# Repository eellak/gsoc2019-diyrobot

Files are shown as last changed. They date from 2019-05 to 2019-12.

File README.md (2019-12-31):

:rocket: GSOC 2019 - A DIY robot kit for educators 
===============

## Introduction
With this project I designed an easy to assembly and program, robot from scratch. The designs are 3D printable and all the electronics parts are easy to find in any electronic equipment store. The robot has the  Raspberry Pi 3+  as the main computer with Raspbian operating system combined with Jupyter Notebook as programing interface and a Node.js application as front-end main control page. You can program and control the robot through your browser using the Proteas wireless access point. 

[View the project on Google Summer of Code website](https://summerofcode.withgoogle.com/projects/#6536613096587264).

You can see the detailed timeline [here](https://github.com/eellak/gsoc2019-diyrobot/blob/master/gsoc-timeline.md).

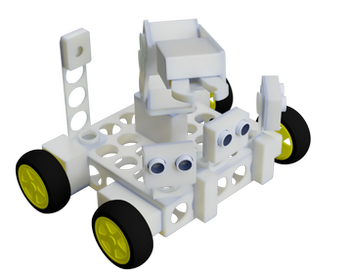
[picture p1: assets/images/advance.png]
proteas robot advance


### Proteas robot teaser video

(http://www.youtube.com/watch?v=83zVe_P6pcM "")

Final Report
------------

You can visit this [gist](https://gist.github.com/chronis10/9d069c56b3df9c92693ac8d24270a62a) that summarizes in a few words, the work which was done during the Google Summer of Code working period.

Synopsis
--------

With this project you can construct a modular robot, easy to use with cheap electronic parts and 3D printed parts. The procedure to construct the robot is explained detailed on the [Wiki](https://github.com/eellak/gsoc2019-diyrobot/wiki) of the project. The main procedure is:

1. Read the wiki and choose the type of robot you want
2. Gather all the needed electronic parts
3. Print the parts
4. Preassembly the blocks
5. Burn the custom Raspbian image and load it to the Raspberry PI
6. Assembly the robot
7. Power on the robot 
8. Connect to proteas network and have fun.

Challenges -> Problems -> Solutions
--------

The main challenge of the project was the requirement to avoided the usage of tools on the assembly stage. The first days of the project I designed and tested about ten different designs of the socket system. Another problem was the voltages of the electronic parts, most of the parts are designed to work with the Arduino 5V voltages but the Raspberry Pi voltages are 3V and for that reason used a Bidirectional Logic Level Converter.  Also the investigation of a stable and capable power source  was crucial because nobody wants a robot with short working time, finally selected a custom build power block (BMS, Li-ion batteries and stepdown circuit) which offers excellent performance, recharging capability, usage of the robot with external power supply and long working time. Finally because the robot needed to be easy to programme form people with low experience with programming, decided to use a object oriented way. The code for the electronic parts in some cases it was complicated for a new user and using the object oriented way the code transformed from 50 lines to 3 lines easy to understand and use code. 

GSoC Deliverables
------------

1. 3D printed parts ready to print
2. Python library for easy usage and control of the robot
3. Integration with Jupyter
4. Easy way to access the robot
5. Custom Raspbian image with OpenCV, Jupyter, Node.js, Python libraries, instructions and configuration intergraded.
6. Extensive instruction for the assembly and usage
7. Jupyter Notebooks with examples and educational material

Future Work
------------

There is still a lot work that may be done, in order the Proteas robot to be a direct competitive to any commercial alternative on education robotics and I believe, with the support of the Open Source community, that goal can be reached. Feel free, to contribute and participate on that project, any suggestion and improvement are welcomed. 

Some thoughts for future work:

1. Support of analogue sensors
2. More 3D printed components
3. More electronic sensors support
4. Improvements on designs
5. Integration with Scratch, Node-RED
6. Compatibility with Arduino
7. Better wireless connection 
8. Companion app for Android/IOS
9. Custom build PCB for easy connection of the electronic components

### Student

* [Christos Chronis](https://github.com/chronis10)

### GSoC Mentors

* Iraklis Varlamis
* Theodoros Karounos
* Konstantinos Kalovrektis

### Organization :  Open Technologies Alliance - GFOSS 

<br />The 3D designs , educational material and text is licensed under a  <a rel="license" href="http://creativecommons.org/licenses/by-nc/4.0/">Creative Commons Attribution-ShareAlike 4.0 International License</a>

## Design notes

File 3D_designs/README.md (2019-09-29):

# The designs of the DIY-Robot kit

Here you can find all the stl files for the kit. For instructions and images visit the [Wiki](https://github.com/eellak/gsoc2019-diyrobot/wiki)  of the repository . 

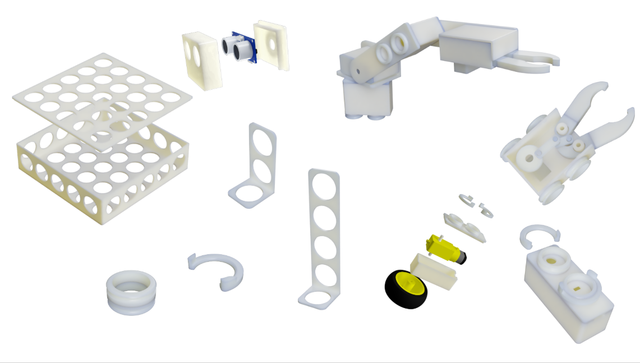
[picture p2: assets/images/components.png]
components


* Socket System templates 
  * Connection System between components blocks :white_check_mark:
  * Lock System between for components blocks :white_check_mark:
  * Raspberry Pi 3 self lock base :white_check_mark:
  * L298N Dual H-Bridge self lock base :white_check_mark:
* Motor Block 
  * Top part :white_check_mark:
  * Bottom part :white_check_mark:
* Free rotation modules
  * Metal Ball Caster :white_check_mark:
  * Free rotation wheel module :white_check_mark:
* Main body 
  * Top part :white_check_mark:
  * Bottom part tall :white_check_mark:
  * Bottom part short:white_check_mark:
* Boards modules
  * Raspberry Pi 3 self lock base with male socket :white_check_mark:
  * L298N Dual H-Bridge self lock base with male socket :white_check_mark:
  * Power block 
  * Battery block
* Wire grouping socket 
  
  * 8 Pin expansion suitable for GND and VCC  :white_check_mark:
  * 10 cables management component (thin cables) :white_check_mark:
  * 10 cables management component (normal cables) :white_check_mark:
  * 10 cables management component (mixed cables) :white_check_mark:
* Servo Blocks
  
  * SG-5010 Servo :white_check_mark:
* Arm parts
  * Rotation base :white_check_mark:
  * Arm extension servo head socket :white_check_mark:
  * Robotic Arm Gripper :white_check_mark:
* Sensors Blocks
  * Raspberry Pi Camera Block :white_check_mark:
  
  * Ultrasonic sensor HC-SR04 :white_check_mark:
  
  * IR Infrared Obstacle :white_check_mark:
  
  * Sensor extender 2 socket L shape:white_check_mark:
  
  * Sensor extender 4 socket L shape:white_check_mark:
  
  * Dual male connector for Sensor extenders :white_check_mark:
  
  * Breadboard module :white_check_mark:
  
  * Magic Super-Mini-Breadboard :white_check_mark:
  
  * Nokia 5110 LCD screen module :white_check_mark:
  
  * Optical odometer HC-020K block:white_check_mark:
  
  * Internal Optical odometer HC-020K block:white_check_mark:

## Explanation of the marks
* :warning: Under Construction part, not ready for printing yet.
* :white_check_mark: Ready for printing.
* :construction: Upcoming release

<br />The 3D designs , educational material and text is licensed under a  <a rel="license" href="http://creativecommons.org/licenses/by-nc/4.0/">Creative Commons Attribution-ShareAlike 4.0 International License</a>

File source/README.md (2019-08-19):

# The mind of the Robot

Here you can find all the needed files (python libraries and scripts) for a smooth deployment. 

For instructions visit the [Wiki](https://github.com/eellak/gsoc2019-diyrobot/wiki) of the repository

An overview of my programming stuck.
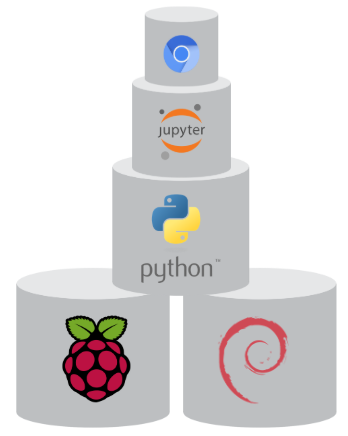
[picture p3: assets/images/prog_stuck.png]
prog stuck


* Python robot library :white_check_mark::
  * Buzzer class :white_check_mark:
  * Dc motor class :white_check_mark:
  * Optical odometer class :white_check_mark:
  * Obstacle IR sensor  class :white_check_mark:
  * Servo motor class :white_check_mark:
  * Nokia 5110 screen :white_check_mark:
  * MPU6050 accelerometer :white_check_mark:
  * Ultrasonic sensor :white_check_mark:
  * General input class (every sensor with digital output eg. light sensor) :white_check_mark:
  * General output class (led and every sensor with digital input eg.  relay shield) :white_check_mark:
  * Button class with software Pull Down parameter enabled :white_check_mark:
  * Timer class for usage on PID,logs or every usage with time elapsed needs :white_check_mark:
  * Log data class store data for plot or evaluation :white_check_mark:
  * Make csv class save measurements to csv :white_check_mark:
  * PID class :white_check_mark:
  * Inverse Kinematics for 2-DOF robotic arm :white_check_mark:
  
* Computer Vision library :white_check_mark:
  * Capture image class :white_check_mark:
  * Image preview class on Jupyter notebook :white_check_mark:
  * Aruco artifacts class :white_check_mark:
  * Line follower class (camera mode) :white_check_mark:
  * Face detection class  :white_check_mark:
  * Follow the target class (line,face or Aruco artifact) :white_check_mark:
  * Approach the target class (face or Aruco artifact) :white_check_mark:
  
* Notebooks section
  * Courses and Examples :white_check_mark:

* Browser interface
  * Node.js app for the robot management from your browser.:white_check_mark:

## :exclamation: **Important Notice** :exclamation:
:cop: The robot fully comply with the three laws of robotics:

**Asimov's Laws**

  * **First Law:** A robot may not injure a human being or, through inaction, allow a human being to come to harm.
  * **Second Law:** A robot must obey the orders given it by human beings except where such orders would conflict with the First Law.
  * **Third Law:** A robot must protect its own existence as long as such protection does not conflict with the First or Second Laws.

## Explanation of the marks
* :warning: Under Construction, probably errors not ready for use.
* :white_check_mark: Ready for usage.
* :construction: Upcoming release

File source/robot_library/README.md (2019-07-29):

## GSOC 2019 - A DIY robot kit for educators

The proteas library is a python robotics library for 
Raspberry Pi. This library created for the "GSOC 2019 - A DIY robot kit for educators" 
by Christos Chronis. This library mainly designed to work along the Jupyter Notebook
but works fine direct from any python script. You can easly control all the electronics
parts of a robot with minimun requirement the GPIO pin number. In the library you can also find 
some applications of computer vision with OpenCV, such as face detection, arruco artifact detection
e.t.c.. More informations on https://github.com/eellak/gsoc2019-diyrobot.

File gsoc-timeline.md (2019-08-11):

## :calendar: Timeline

The implementation details follow, organized by [GSoC timeline](https://developers.google.com/open-source/gsoc/timeline).

## Phase 1 (May 27 - Jun 28)

The proper electronic parts selected for that project and  designed,printed and tested the 3D parts of the robot in a modular way with a tool-less philosophy. 

- Selection of electronic parts
- 3D designs :triangular_ruler:
- Parts printing stage
- Functionality tests of the parts
- Robot Assembly :wrench:

## Phase 2 (Jun 29 - Jul 26)

New libraries created for the communication between hardware-software.  A object oriented way for programming selected and the integration with Jupyter completed. 

- Control library
- Vision library
- OpenCV integration
- Special control and functionality library (e.x. PID Controller)
- Jupyter Notebook integration
- Wireless access, control and programming of the program achieved 

## Phase 3 (Jul 27 - Aug 26)

All the needed preparations completed  for easy deployment of software and material for the courses, user manuals and instructions created.

- Modifications of Rasbian image
- Courses on Jupyter Notebook (e.x. Line Follower robot)
- PDFs with extensive instructions for the assembly and usage of the robot
- Final debugging
- Wiki page created

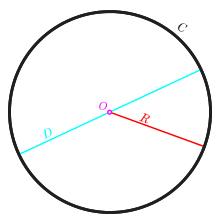
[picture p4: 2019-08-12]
source/notebooks/Courses/Distance calculation based on circle theory/images/circle.png

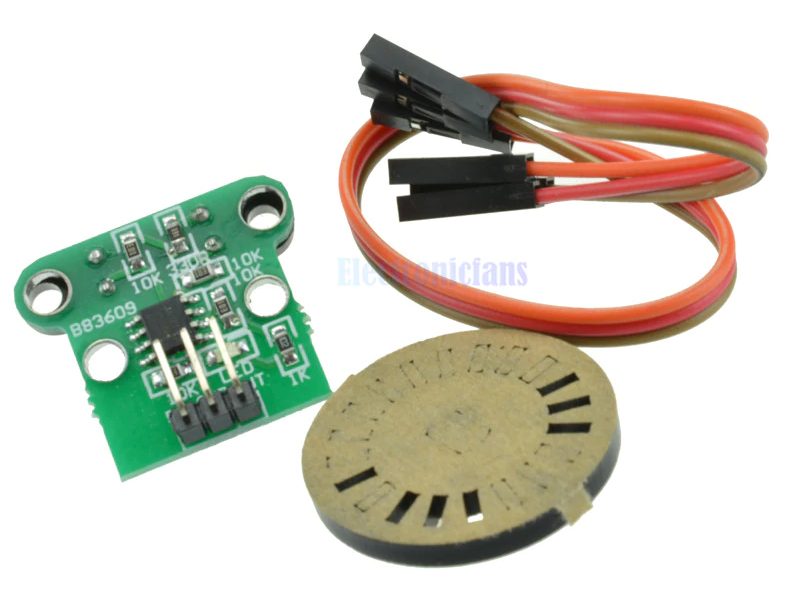
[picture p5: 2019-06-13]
3D_designs/odometers/optical_odometer_block/HC-020K.png

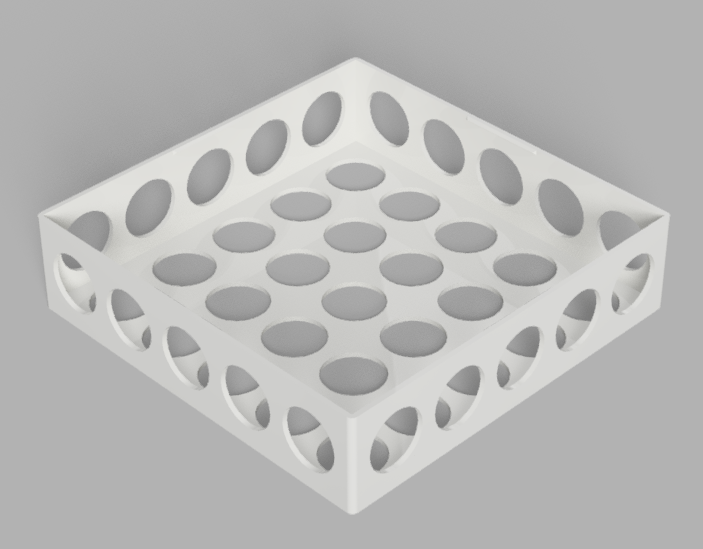
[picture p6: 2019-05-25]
3D_designs/base/main_body_bottom_short_v1.png

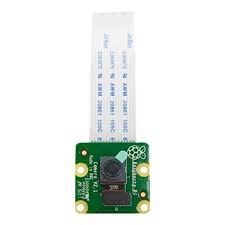
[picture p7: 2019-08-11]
3D_designs/raspberry_pi_camera_block/raspberry pi camera.jpg

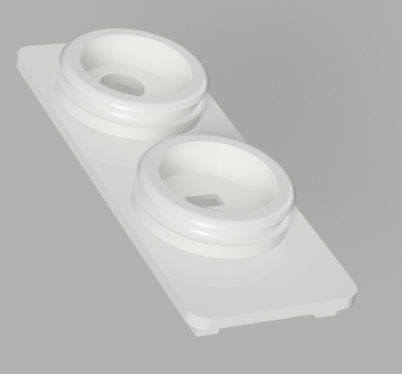
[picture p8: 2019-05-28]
3D_designs/motor_block/motor_block_top_v1.png

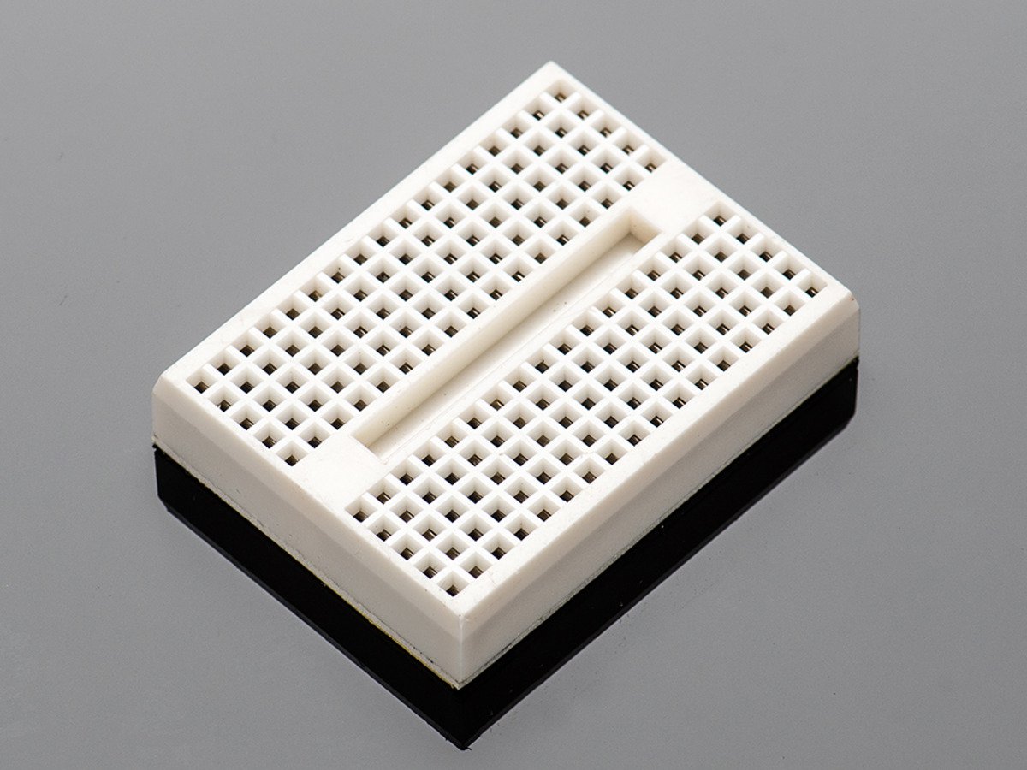
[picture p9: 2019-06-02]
3D_designs/breadboard_blocks/small_breadboard_block/breadboard.jpg

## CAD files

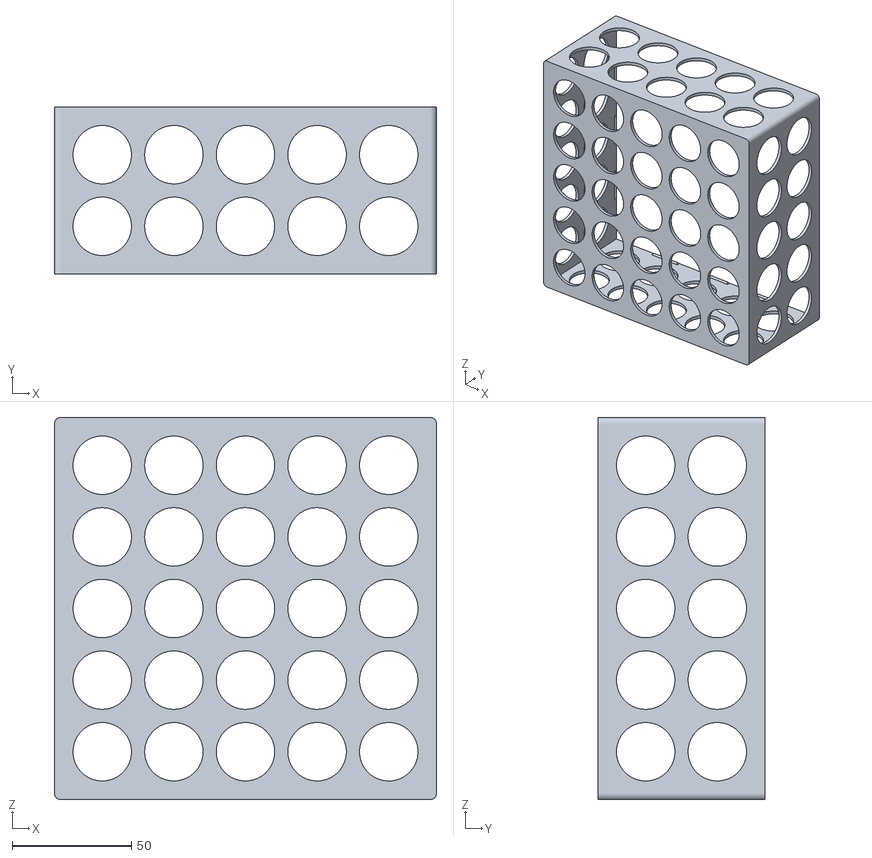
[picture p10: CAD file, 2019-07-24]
3D_designs/base/main_body_bottom_tall_v1.stl
160.0 x 70.0 x 160.0

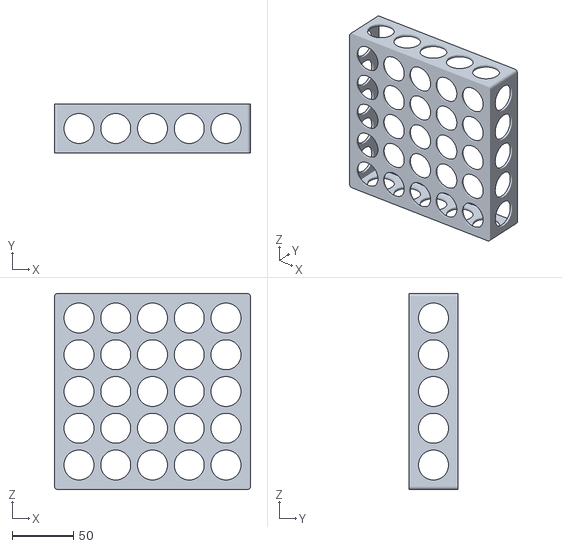
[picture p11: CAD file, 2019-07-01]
3D_designs/base/main_body_bottom_short_v1.stl
160.0 x 40.0 x 160.0

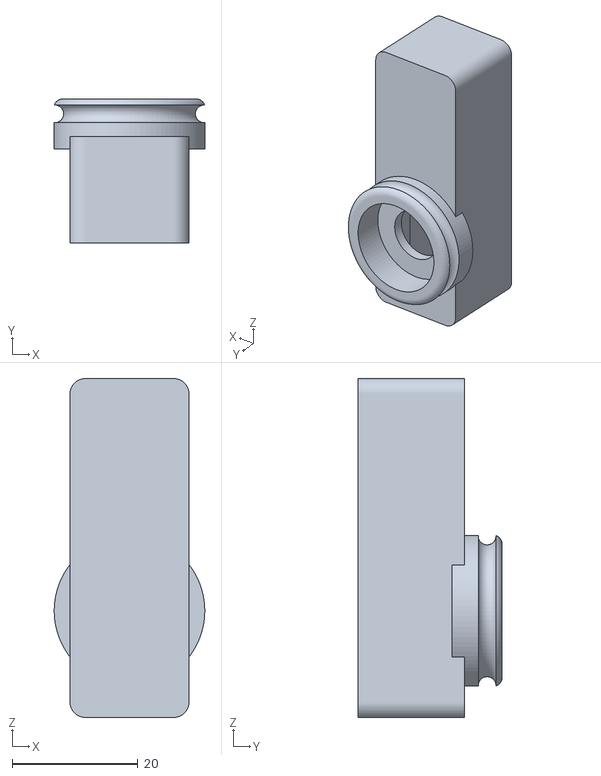
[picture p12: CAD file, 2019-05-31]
3D_designs/ir_obstacle_sensor_block/ir_block_assembled_v1.stl
24.0 x 23.0 x 54.0

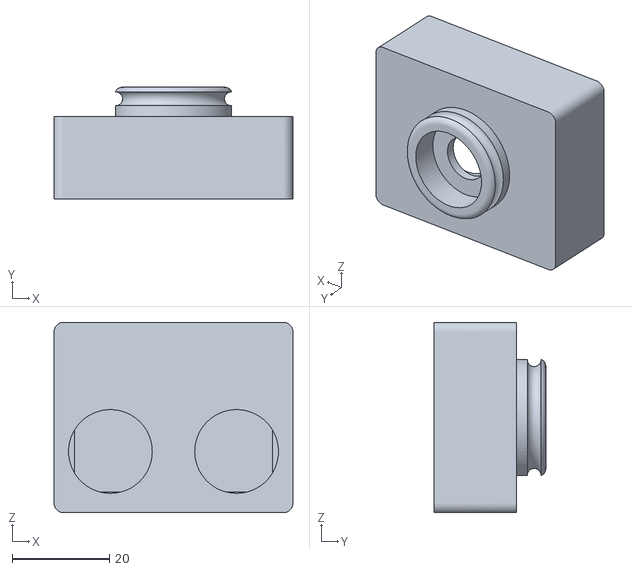
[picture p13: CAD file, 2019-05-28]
3D_designs/ultrasonic_sensor_block/HC-SR04_ultrasonic_block_assembled_v1.stl
49.2 x 23.0 x 39.2

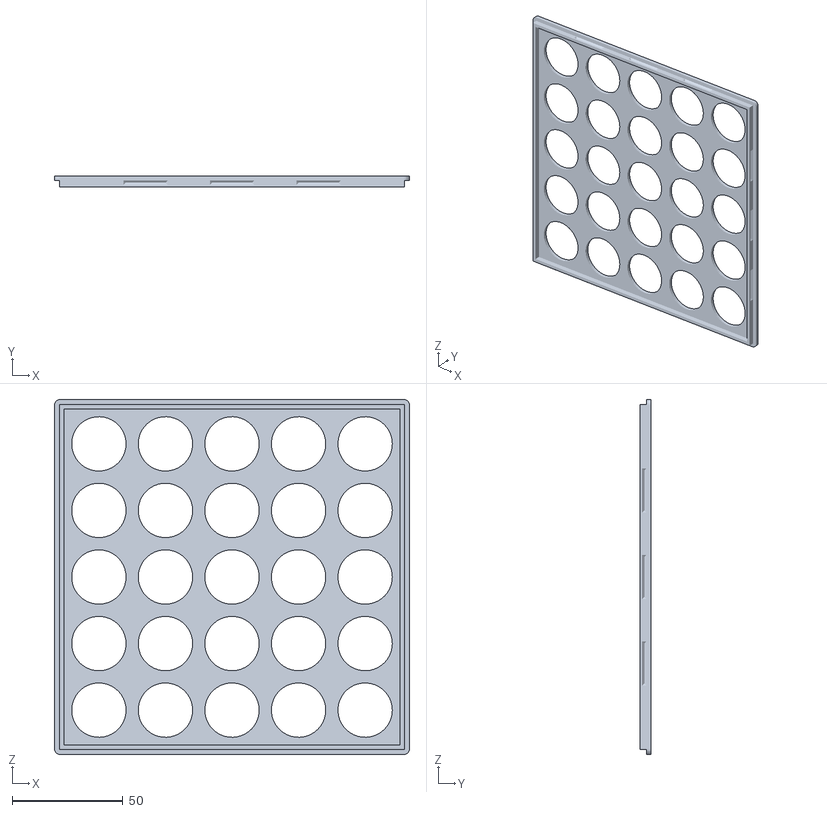
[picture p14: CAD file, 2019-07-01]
3D_designs/base/main_body_top_v1.stl
160.0 x 5.00 x 160.0

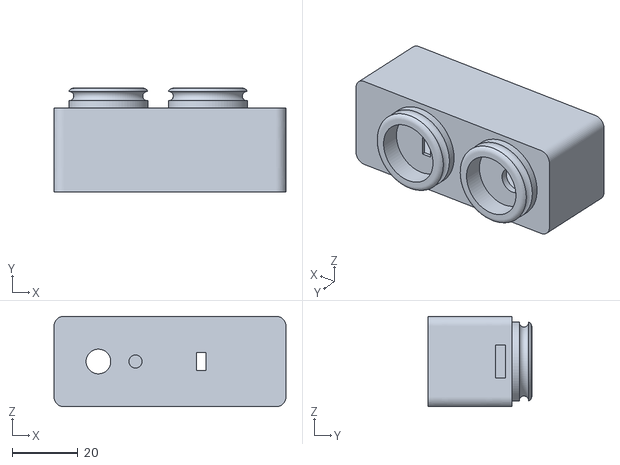
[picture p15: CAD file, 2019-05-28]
3D_designs/motor_block/motor_block_assembled_v1.stl
70.5 x 31.5 x 27.5

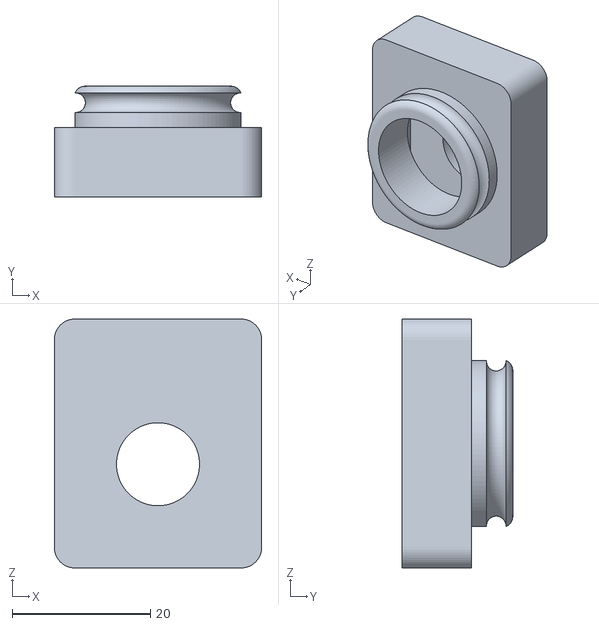
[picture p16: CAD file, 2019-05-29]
3D_designs/raspberry_pi_camera_block/camera_block_assembled_v1.stl
30.0 x 16.0 x 36.0

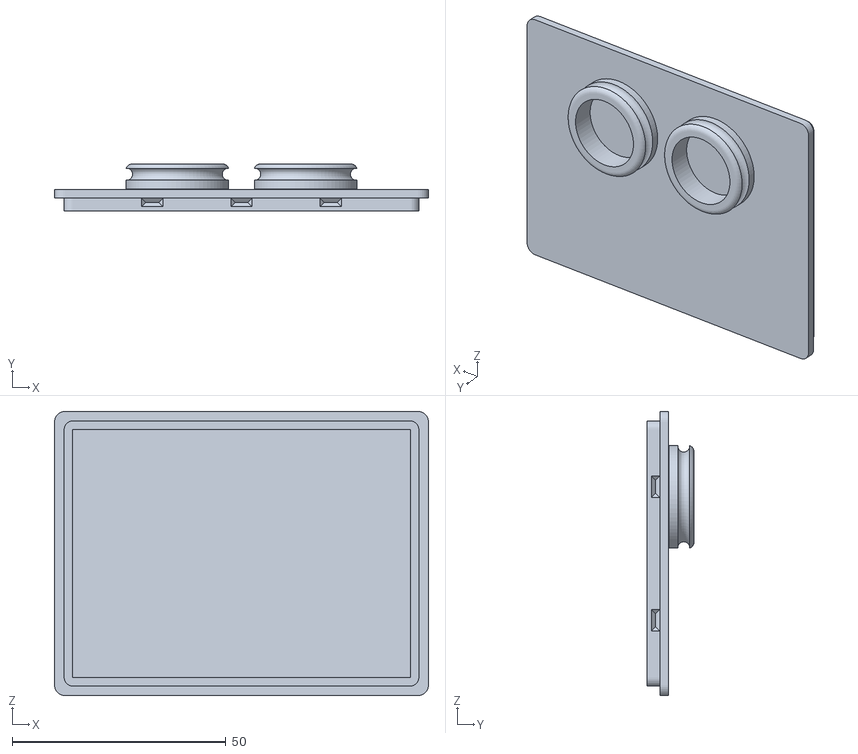
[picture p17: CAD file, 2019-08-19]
3D_designs/battery_block/battery_block_top_v1.stl
87.5 x 11.0 x 66.5

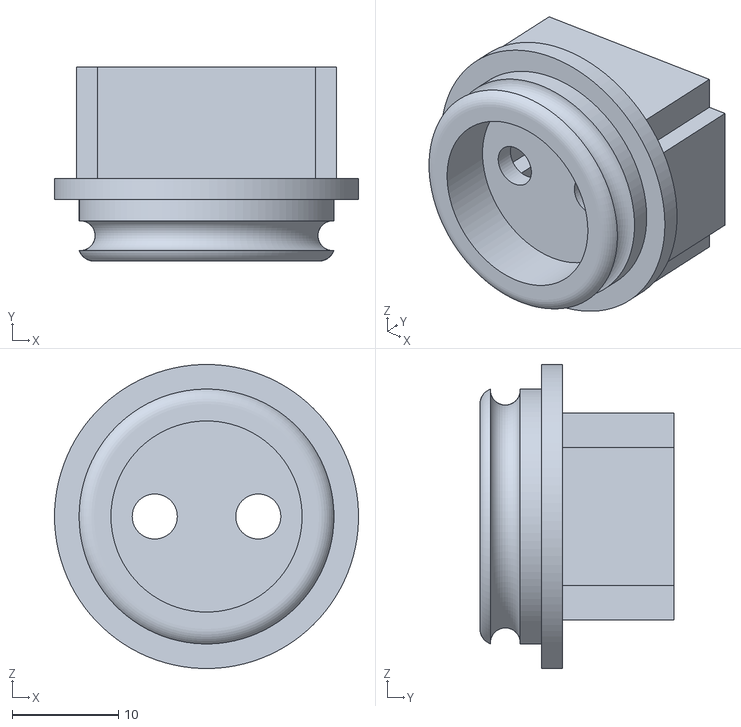
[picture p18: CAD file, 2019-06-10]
3D_designs/breadboard_blocks/mini_breadboard_block/mini_breadboard v1.stl
28.6 x 18.3 x 28.6

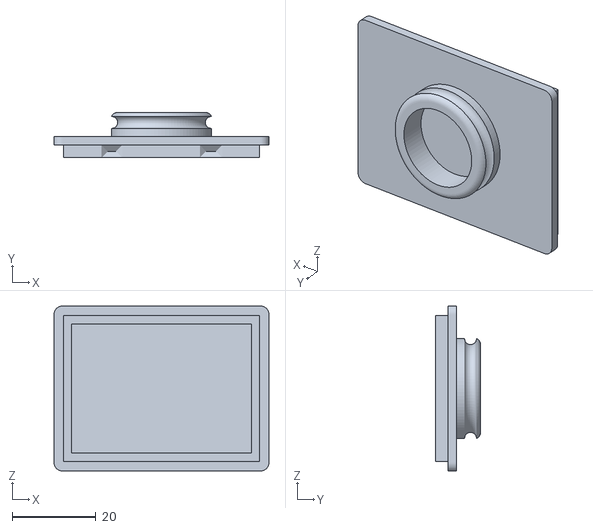
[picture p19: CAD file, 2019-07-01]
3D_designs/breadboard_blocks/small_breadboard_block/breadboard_module_top_v1.stl
51.5 x 10.8 x 39.5

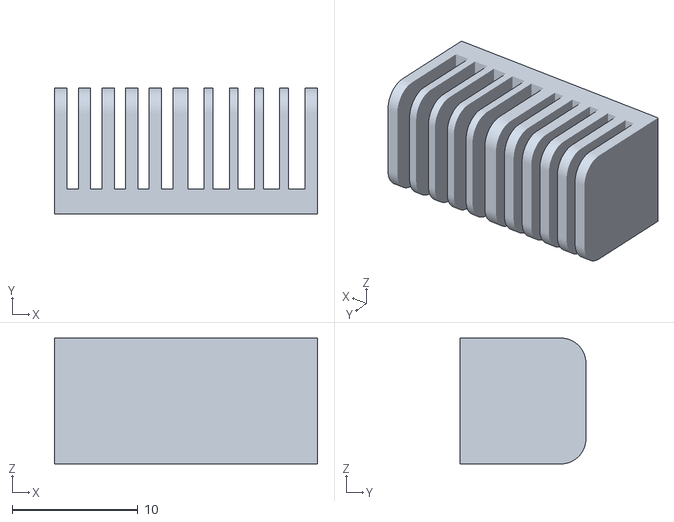
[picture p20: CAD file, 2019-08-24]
3D_designs/cable_management/mixed_cables.stl
20.9 x 10.0 x 10.0

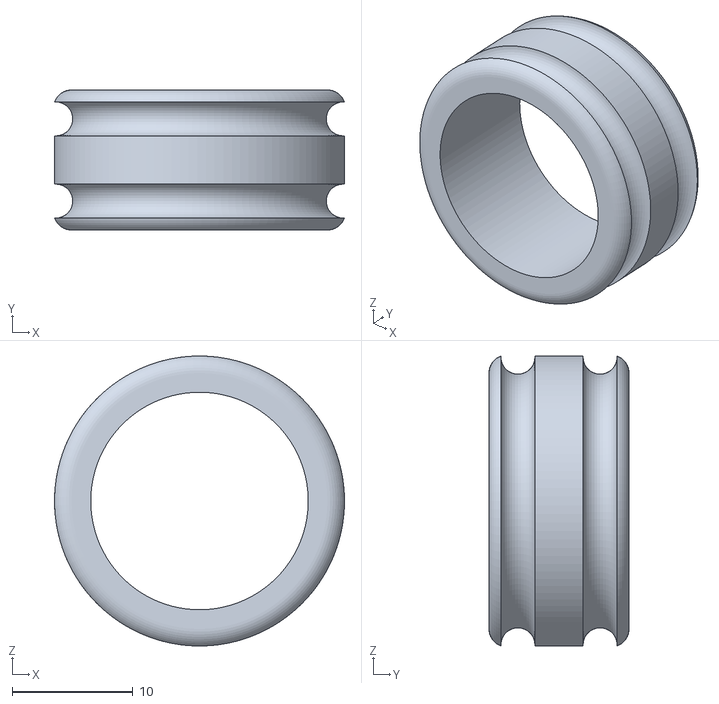
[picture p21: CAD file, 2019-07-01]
3D_designs/expansion_parts/dual_male_head_v1.stl
24.0 x 11.6 x 24.0

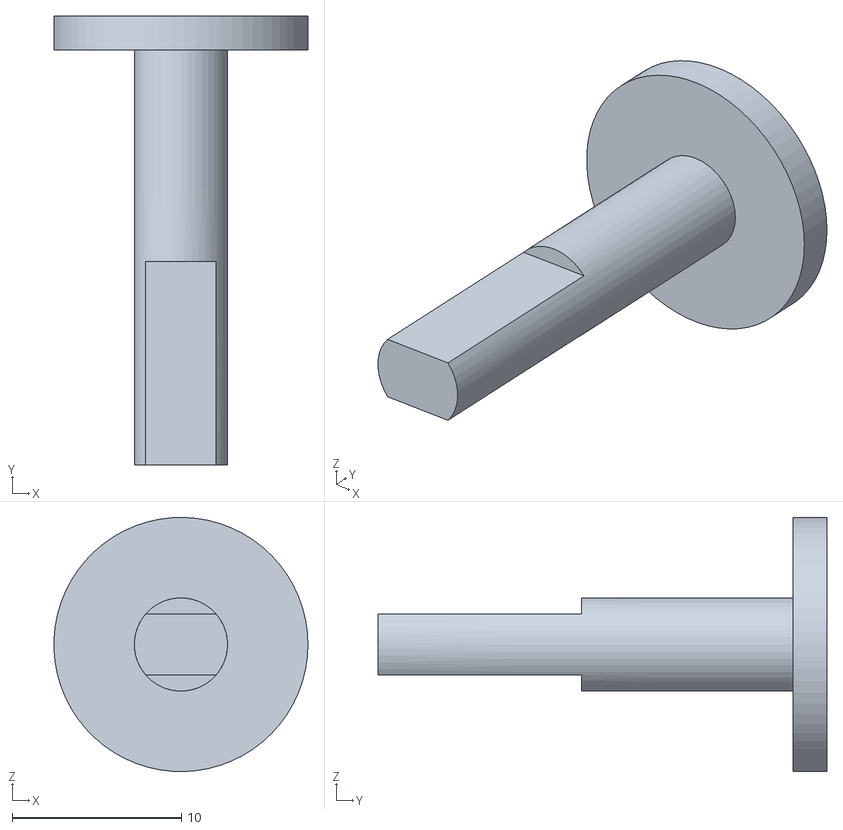
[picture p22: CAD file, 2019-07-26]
3D_designs/free_rotation_parts/free_rotation_wheel_block/shaft_v1.stl
15.0 x 26.5 x 15.0

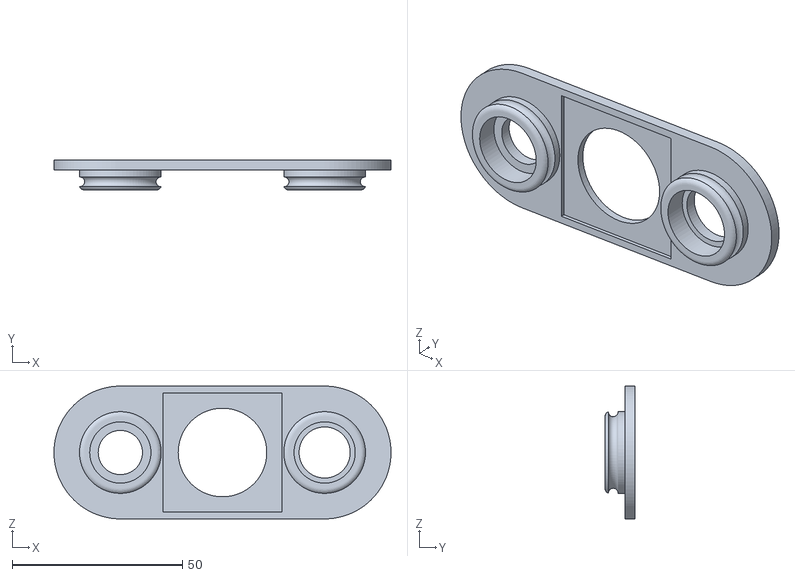
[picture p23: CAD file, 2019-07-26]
3D_designs/free_rotation_parts/metal_ball_caster_block/metal_ball_caster_v1.stl
99.0 x 8.80 x 39.0

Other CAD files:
3D_designs/ir_obstacle_sensor_block/ir_block_top_v1.stl
3D_designs/motor_block/motor_block_bottom_v1.stl
3D_designs/motor_driver_base/L298N_Dual_H-Bridge_clip_module_v1.stl
3D_designs/multiconnector_module/multiconnector_module_v1.stl
3D_designs/battery_block/battery_block_bottom_v1.stl
3D_designs/breadboard_blocks/small_breadboard_block/breadboard_module_bottom_v1.stl
3D_designs/cable_management/normal_cables.stl
3D_designs/cable_management/thin_cables.stl
3D_designs/expansion_parts/sensor_extender_tall_v1.stl
3D_designs/expansion_parts/sensor_extender_v1.stl
3D_designs/free_rotation_parts/free_rotation_wheel_block/free_rotation_wheel_block_v1.stl
3D_designs/ir_obstacle_sensor_block/ir_block_bottom_v1.stl
3D_designs/motor_block/motor_block_top_v1.stl
3D_designs/nokia_5110_screen_block/screen_block_bottom_v1.stl
3D_designs/nokia_5110_screen_block/screen_block_top_v1.stl
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

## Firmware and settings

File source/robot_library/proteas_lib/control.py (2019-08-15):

import time
import RPi.GPIO as GPIO
import math
import time
import csv
import Adafruit_Nokia_LCD as LCD
import Adafruit_GPIO.SPI as SPI
from PIL import ImageFont,ImageDraw,Image
from netifaces import interfaces, ifaddresses, AF_INET
import matplotlib.pyplot as plt
from mpu6050 import mpu6050
from random import randrange
import smbus	

# Hardware section
class gen_output():
	'''
	Class gen_output(pin)
	Deafult pin 5
	Functions:
	set_on() set High the output pin
	set_off() set Low the output pin
	'''
	def __init__(self,pin=5):
		self.pin = pin
		GPIO.setup(self.pin,GPIO.OUT)
		GPIO.output(self.pin, False)
	def set_on(self):
		GPIO.output(self.pin, True)
	def set_off(self):
		GPIO.output(self.pin, False)	


class gen_input():
	'''
	Class gen_input(pin)
	Default pin 4
	Functions:
	get_state() return True/False
	'''
	def __init__(self,pin=4):
		self.pin = pin
		GPIO.setup(self.pin,GPIO.IN)
	def get_state(self):
		return GPIO.input(self.pin)

class button():
	'''
	Class button(pin)
	Default pin 18
	Software pull down activated
	Functions:
	get_state() return True/False
	'''
	def __init__(self,pin=18):
		self.pin = pin
		GPIO.setup(self.pin,GPIO.IN,pull_up_down=GPIO.PUD_UP)
	def get_state(self):
		return GPIO.input(self.pin)


class ultrasonic_sensor():
	'''
	Class ultrasonic_sensor(echo_pin,trig_pin)
	Default pins echo_pin=14,trig_pin=15
	Functions:
	get_distance() return distance on cm
	'''
	def __init__(self,echo_pin=14,trig_pin=15):
		self.echo_pin = echo_pin
		self.trig_pin = trig_pin
		GPIO.setup(self.echo_pin,GPIO.IN)
		GPIO.setup(self.trig_pin,GPIO.OUT)
		GPIO.output(self.trig_pin, False)
	def get_distance(self):

		GPIO.output(self.trig_pin, True)
		time.sleep(0.00001)
		GPIO.output(self.trig_pin, False)
		StartTime = time.time()
		StopTime = time.time()
		while GPIO.input(self.echo_pin) == 0 :
			StartTime = time.time()

		while GPIO.input(self.echo_pin) == 1:
			StopTime = time.time()
		TimeElapsed = StopTime - StartTime
		distance = (TimeElapsed * 34300) / 2
		return distance

class screen():
	'''
	Class screen(SCLK = 21,DIN = 20,DC = 16,RST =7,CS = 12)
	Functions:
	clear_scrn() Clears the screen
	show_text(text,x=0,y=0) Prints text in the screen
	ip_screen() Prints the current ip
	print_text(text_list) Get a list input of 5 item and print every item in a line
	show_image(path) Draw a graph in png from the images/ path
	'''
	def __init__(self,SCLK = 21,DIN = 20,DC = 16,RST =7,CS = 12):
		self.SCLK = SCLK
		self.DIN = DIN
		self.DC = DC
		self.RST = RST
		self.CS = CS
		self.disp = LCD.PCD8544(DC, RST, SCLK, DIN, CS)
		self.disp.begin(contrast=60)
		self.font = ImageFont.load_default() #ImageFont.truetype('Minecraftia.ttf', 8)
		self.clear_scrn()
		self.empty_canvas()

	def clear_scrn(self):
		self.disp.clear()
		self.disp.display()
	def empty_canvas(self):
		self.canvas= Image.new('1', (LCD.LCDWIDTH, LCD.LCDHEIGHT))
		self.draw = ImageDraw.Draw(self.canvas)
		self.draw.rectangle((0,0,LCD.LCDWIDTH,LCD.LCDHEIGHT), outline=255, fill=255)

	def show_text(self,text,x=0,y=0):
		self.draw.text((x,y),text, font=self.font)

	def show_canvas(self):
		self.disp.image(self.canvas)
		self.disp.display()
	def ip_screen(self):
		self.clear_scrn()
		self.empty_canvas()
		self.show_text("Proteas Robot")
		ipl = get_ip()
		self.show_text("Connect to:",0,9)
		self.show_text("http://",0,19)
		self.show_text(ipl[-1],0,29)
		self.show_text(":8080",0,39)
		self.show_canvas()

	def print_text(self,text_list):
		self.clear_scrn()
		self.empty_canvas()
		posy = 0
		for i in range(0,5):
			temp  = text_list[i]
			if isinstance(temp,int) or isinstance(temp,float):
				temp = str(temp)
			self.show_text(temp,0,posy)
			posy += 9
		self.show_canvas()
	def show_image(self,path):
		path = "images/" +path
		self.clear_scrn()
		im = Image.open(path)
		self.canvas = im.resize((LCD.LCDWIDTH, LCD.LCDHEIGHT), Image.ANTIALIAS).convert('1')
		self.show_canvas()


class accelerometer():
	'''
	Class accelerometer(address=0x68)
	Functions:
	get_acceleration(dimension = "all") with "parameter return dictionary with x,y,z acceleration for a specific dimension give as parameter "x","y","z" return value
	get_gyro(dimension = "all") with "parameter return dictionary with x,y,z acceleration for a specific dimension give as parameter "x","y","z" return value
	'''
	def __init__(self,address=0x68):
		self.sensor = mpu6050(address)
	def get_acceleration(self,dimension = "all" ):
		accel = self.sensor.get_accel_data()
		if dimension == "all":
			return accel
		elif dimension == "x" or dimension == "y" or dimension == "z":
			return accel[dimension]
		else:
			print("Dimension not recognized!!")
			return 0
	def get_gyro(self,dimension = "all" ):
		gyro = self.sensor.get_gyro_data()
		if dimension == "all":
			return gyro
		elif dimension == "x" or dimension == "y" or dimension == "z":
			return gyro[dimension]
		else:
			print("Dimension not recognized!!")
			return 0




class buzzer():
	'''
	Class buzzer(pin,freq=1500,dc=50)
	Functions:
	beep() Short tone
	timer(count) Timer function with wait and for every 1 sec makes a tone
	'''
	def __init__(self,pin,freq=1500,dc=50):
		GPIO.setup(pin,GPIO.OUT)
		self.buz = GPIO.PWM(pin,freq)
		self.freq = freq
		self.dc = dc
		self.buz.start(0)
	def beep(self):
		self.buz.ChangeDutyCycle(self.dc)
		time.sleep(0.1)
		self.buz.ChangeDutyCycle(0)
	def timer(self,count):
		print("Timer start for {}".format(count))
		for i in range(1,count+1):
			self.buz.ChangeDutyCycle(self.dc)
			time.sleep(0.5)
			self.buz.ChangeDutyCycle(0)
			time.sleep(0.5)
			print("{} sec".format(i))
		print("Timer finished")
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

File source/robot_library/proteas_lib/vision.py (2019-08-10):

import numpy as np
import cv2, PIL
from cv2 import aruco
import matplotlib.pyplot as plt
import matplotlib as mpl
from IPython.display import display, HTML,clear_output
import PIL.Image

class aruco_find():
	def __init__(self):
		self.aruco_dict = aruco.Dictionary_get(aruco.DICT_6X6_250)
		self.parameters =  aruco.DetectorParameters_create()
		self.ids = []
		self.corners = []
		self.cx = 0
		self.cy = 0
		self.width = 0
		self.height=0		
	def to_gray(self,image):
		return cv2.cvtColor(image, cv2.COLOR_BGR2GRAY)
	def detect(self,image):
		corners, ids, rejectedImgPoints = aruco.detectMarkers(image, self.aruco_dict, parameters=self.parameters)
		return corners, ids, rejectedImgPoints
	def mark_image(self,image,corners, ids):
		if ids is not None:
			self.ids = self.marks_to_list(ids)
			self.corners = self.marks_to_list(corners)
		else:
			self.ids = []
			self.corners = []
		image_marked = aruco.drawDetectedMarkers(image.copy(), corners, ids)
		return image_marked
	def detect_artifacts(self,image):
		gray = self.to_gray(image)
		corners, ids, rejectedImgPoints = self.detect(gray)
		final = self.mark_image(image,corners, ids)
		return final
	def marks_to_list(self,nplist):
		temp = []
		nplist = np.array(nplist).tolist()
		for item in nplist:
			temp.append(item[0])
		return temp
	def find(self,ar_id):
		if len(self.ids)>0:
			if ar_id in self.ids:
				i = self.ids.index(ar_id)
				x1=self.corners[i][0][0]
				x2=self.corners[i][1][0]
				y1=self.corners[i][0][1]
				y2=self.corners[i][3][1]
				self.cx = int(((x2-x1)/2)+x1)
				self.cy = int(((y2-y1)/2)+y1)
				self.width = x2-x1
				self.height = y2-y1		
		else:
				self.cx = 0
				self.cy = 0
				self.width = 0
				self.height = 0
	def mark_frame(self,frame):
		height, width, channels = frame.shape
		cv2.line(frame,(self.cx,0),(self.cx,height),(255,0,0),1)
		cv2.line(frame,(0,self.cy),(width,self.cy),(255,0,0),1)
		return frame
	def get_pos(self):
		return self.cx,self.cy
	def get_rect(self):
		return self.width,self.height

class camera():	
	def __init__(self,camera=0):
		self.camera = camera
		self.cap = cv2.VideoCapture(self.camera)		
	def take_frame(self):
		ret, frame = self.cap.read()
		return frame
	def stop(self):
		self.cap.release()

class show_image():
	def __init__(self,jupyter=True):
		self.jupyter = jupyter
	def cpreview(self,frame):
		cv2.imshow('frame',frame)
		cv2.waitKey(1) 
	def jpreview(self,frame):
		im = cv2.cvtColor(frame, cv2.COLOR_BGR2RGB)
		display(PIL.Image.fromarray(im))		
		clear_output(wait=True)	
	def preview(self,frame):
		if self.jupyter:
			self.jpreview(frame)
		else:
			self.cpreview(frame)
	def clear(self):
		if self.jupyter:	
			clear_output(wait=True)	
		else:
			cv2.destroyAllWindows()

class face_detection():
	def __init__(self):
		cascPath = '/home/pi/ext/haarcascade_frontalface_default.xml'
		self.faceCascade = cv2.CascadeClassifier(cascPath)
		self.cx = 0
		self.cy = 0
		self.width = 0
		self.height=0
		self.faces_num = 0
	def detect_face(self,frame):
		gray = cv2.cvtColor(frame, cv2.COLOR_BGR2GRAY)
		faces = self.faceCascade.detectMultiScale(gray,
		scaleFactor=1.1,
		minNeighbors=5,
		minSize=(30, 30),
		flags=cv2.CASCADE_SCALE_IMAGE)
		if len(faces) > 0:
			self.faces_num = len(faces)
			(x,y,w,h)= faces[0]
			cv2.rectangle(frame, (x, y), (x+w, y+h), (0, 255, 0), 2)
			self.cx = int(((w/2)+x))
			self.cy = int(((h/2)+y))
			self.width = w
			self.height = h
			fheight, fwidth, channels = frame.shape
			cv2.line(frame,(self.cx,0),(self.cx,fwidth),(255,0,0),1)
			cv2.line(frame,(0,self.cy),(fwidth,self.cy),(255,0,0),1)
			cv2.circle(frame,(self.cx, self.cy), 5, (0,255,0), -1)
		else:
			self.faces_num = 0
			self.cx = 0
			self.cy = 0
			self.width = 0
			self.height = 0
		return frame
	def get_faces(self):
		return self.faces_num
	def get_pos(self):
		return self.cx,self.cy
	def get_rect(self):
		return self.width,self.height

class robot_center():
	def __init__(self,width=640):
		self.width = width
		self.step = int(width/5)
		self.w1 = self.step*2
		self.w2 = self.step*3
		
	def direction(self,posx):
		if posx >0 and posx < self.w1:
			print("Go Right")
			return 2
		elif posx >self.w2 and posx < self.width:
			print("Go Left")
			return 1
		elif posx == 0:
			print("No detection")
			return -1
		else:
			print("Stay")
			return 0

class robot_follow():
	def __init__(self,width=640):
		self.width = width
		self.max= int(width/2)
	def direction(self,rx):
		if rx < self.max and rx > 0:
			print("Forward")
			return 1
		elif rx > (self.max + 30):
			print("Back")
			return 2
		elif rx == 0:
			print("No detection")
			return -1
		else:
			print("Stay")
			return 0



class line_follower():
	def __init__(self,width=640,height=480,w=160,h=60):
		self.width = width
		self.height = height
		self.cx = 0
		self.cy = 0
		self.x1 = max(0,int((self.width/2) - (w/2)))
		self.x2 = min(int((self.width/2) + (w/2)),self.width)
		self.y1 = max(0,int((self.height/2) - (h/2)))
		self.y2 = min(int((self.height/2) + (h/2)),self.height)

	def detect_line(self,frame):	
		crop_img = frame[self.y1:self.y2, self.x1:self.x2]
		gray = cv2.cvtColor(crop_img, cv2.COLOR_BGR2GRAY)
		blur = cv2.GaussianBlur(gray,(5,5),0)
		ret,thresh = cv2.threshold(blur,60,255,cv2.THRESH_BINARY_INV)
		contours,hierarchy = cv2.findContours(thresh.copy(), 1, cv2.CHAIN_APPROX_NONE)
		if len(contours) > 0:
			c = max(contours, key=cv2.contourArea)
			M = cv2.moments(c)
			if M['m00'] != 0:
				self.cx = int(M['m10']/M['m00'])
				self.cy = int(M['m01']/M['m00'])
				cv2.line(crop_img,(self.cx,0),(self.cx,self.height),(255,0,0),1)
				cv2.line(crop_img,(0,self.cy),(self.width,self.cy),(255,0,0),1)
				cv2.drawContours(crop_img, contours, -1, (0,255,0), 1)
			else:
				self.cx = 0
				self.cy = 0
		else:
			self.cx = 0
			self.cy = 0

		return crop_img

	def get_pos(self):
		return self.cx,self.cy

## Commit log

2019-05-19 init designs for socket system
    [socket_in_v1.stl, socket_out_v1.stl]
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2019-05-19 init designs for the motor block
    [motor_block_assembled_v1.stl, motor_block_top_v1.stl]
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2019-05-19 motor block bottom
    [motor_block_bottom_v1.stl]
2019-05-21 minor design changes
    [motor_block_bottom_v1.stl]
2019-05-21 minor design changes and socket template added
    [socket_in_v1.stl, socket_template_v1.stl]
2019-05-21 minor design changes for better attachment
    [motor_block_bottom_v1.stl, motor_block_top_v1.stl]
2019-05-22 final designs of some parts and new part added
    [3wire_group_socket_v1.stl, motor_block_assembled_v1.stl, motor_block_top_v1.stl]
2019-05-22 minor changes on design
    [socket_template_v1.stl]
2019-05-23 socket template for raspberry pi 3 base
    [raspberry_pi_3_base_template v1.stl]
2019-05-23 new component added
    [L298N_Dual_H-Bridge_base_template v1.stl]
2019-05-24 main body components added, modification stage
    [main_body_bottom_v1.stl, main_body_top_v1.stl]
2019-05-25 modifications on main body and new components added for expandability and more boards support
    [L298N_Dual_H-Bridge_clip_module_v1.stl, main_body_bottom_v1.stl, main_body_top_v1.stl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]
2019-05-26 durability upgrades
    [L298N_Dual_H-Bridge_clip_module_v1.stl, motor_block_assembled_v1.stl, motor_block_top_v1.stl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]
2019-05-27 ulrasonic sensor module added
    [HC-SR01_ultasonic_module_assembled_v1.stl, HC-SR01_ultasonic_module_bottom_v1.stl, HC-SR01_ultasonic_module_top_v1.stl.stl]
2019-05-28 durability upgrade for socket sytem and lock ring mechanism added
    [motor_block_assembled_v1.stl, motor_block_top_v1.stl, socket_lock_template_v1.stl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]
2019-05-28 modification in all parts for the new socket system
    [HC-SR01_ultasonic_module_assembled_v1.stl, HC-SR01_ultasonic_module_bottom_v1.stl, HC-SR01_ultasonic_module_top_v1.stl.stl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]
2019-05-28 sensor extender and connectors added
    [dual_male_head_v1.stl, sensor_extender_v1.stl]
2019-05-28 deusgns modifications for better fit
    [main_body_bottom_v1.stl, main_body_top_v1.stl, sensor_extender_v1.stl]
2019-05-29 camera block added
    [camera_module_assembled_v1.stl, camera_module_bottom_v1.stl, camera_module_top_v1.stl]
2019-05-30 small modifications
    [motor_block_bottom_v1.stl, motor_block_top_v1.stl]
2019-05-31 modifications on camera modules
    [camera_module_bottom_v1.stl]
2019-05-31 modifications on socket lock
    [socket_lock_template_v1.stl]
2019-05-31 ir obstacle sensor module added
    [ir_module_assembled_v1.stl, ir_module_bottom_v1.stl, ir_module_top_v1.stl]
2019-05-31 corrections and photo of ir sensor
    [HC-SR04_ultasonic_module_assembled_v1.stl, HC-SR04_ultasonic_module_bottom_v1.stl, HC-SR04_ultasonic_module_top_v1.stl.stl]
2019-06-01 modifications for better fit
    [ir_module_top_v1.stl, socket_lock_template_v1.stl]
2019-06-02 breadboard module added
    [breadboard_module_bottom_v1.stl, breadboard_module_top_v1.stl]
2019-06-03 new part added
    [ir_module_top_v1.stl, servo_bottom_large_v1.stl, servo_top_large_v1.stl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]
2019-06-04 rotation base added
    [servo_bottom_large_v1.stl, servo_rotation_base_v1.stl]
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2019-06-06 durability modifications
    [servo_rotation_base_v1.stl]
2019-06-06 arm extensions parts added
    [arm_extension_free_side_v1.stl, arm_extension_servo_head_v1.stl]
2019-06-09 gripper parts added
    [gripper_con1_v1.stl, gripper_con2_v1.stl, gripper_p1_v1.stl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]
2019-06-10 grripper block added
    [claw_left_v1.stl, claw_right_v1.stl, clip_long_v1.stl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]
2019-06-10 alternative servo base added
    [servo_rotation_base_low_prof_v1.stl]
2019-06-10 Magic Super-Mini-Breadboard module added
    [mini_breadboard v1.stl]
2019-06-12 nokia screen module added
    [screen_module_bottom_v1.stl, screen_module_top_v1.stl]
2019-06-13 optical odometer added
    [odometer_bottom_v1.stl, odometer_top_v1.stl, shaft_v1.stl]
2019-06-14 design modifications on odometer
    [odometer_bottom_v1.stl, odometer_top_v1.stl]
2019-07-01 final designs updates
    [HC-SR04_ultasonic_module_top_v1.stl.stl, L298N_Dual_H-Bridge_clip_module_v1.stl, arm_extension_free_side_v1.stl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]
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2019-07-04 8 pin expansion module added
    [pin_expansion.stl]
2019-07-06 bug fixes
    corrections on line follower mode and acceeleration velocity experiment
    [proteas_lib.py]
2019-07-07 line follower bug fixes and compass class added
    [ir_module_top_v1.stl]
2019-07-09 ultasonic sensor get_distance corrections
    [proteas_lib.py]
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2019-07-24 tall bottom body part
    [main_body_bottom_tall_v1.stl]
2019-07-25 free rotation wheel and optical odometer
    [coupler_v1.stl, optical_odometer_body_v1.stl, rotation_body_v1.stl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]
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2019-07-26 free rotation modules added
    [free_rotation_wheel_module_v1.stl, metal_ball_caster_v1.stl, shaft_v1.stl]
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2019-07-27 duplicated files
    [rotation_body_v1.stl, shaft_v1.stl]
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2019-08-05 corrections on control library
    [control.py]
2019-08-11 categorization of the components and better folder structure
    [3wire_group_socket_v1.stl, HC-SR04_ultrasonic_block_assembled_v1.stl, HC-SR04_ultrasonic_block_bottom_v1.stl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]
2019-08-15 new notebooks added and correction on webserver
    [control.py]
2019-08-15 template folder
    [male_socket.f3d, male_socket.obj, socket_clip.f3d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]
2019-08-19 final modifications and corrections
    [battery_block_bottom_v1.stl, battery_block_top_v1.stl, claw_right_v1.stl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]
2019-08-24 cable mangement components
    [mixed_wires.stl, normal_wires.stl, thin_wires.stl]
2019-08-24 new components, cables management components
    [mixed_cables.stl, normal_cables.stl, thin_cables.stl]
2019-08-26 minor modifications
    [socket_clip.f3d, socket_clip.obj, socket_clip_v1.stl]
